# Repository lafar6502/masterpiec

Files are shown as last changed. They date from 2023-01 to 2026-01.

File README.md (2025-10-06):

# masterpiec

## Summary
Masterpiec is an arduino-based pellet and coal burner controller. It automates the burning process and controls temperatures of central heating and hot water boiler. 
The software runs on Arduino Mega 2560 and drives the fuel feeder, blower fan and water pumps (central heating, hot water boiler and hot water circulation). The control is optimized for fuel efficiency and clean burn. Masterpiec can be adapted to multiple types of pellet and coal burners with automatic fuel feed, and is pretty simple to build as a DIY project. 
## 
## Aktualizacje

[Lista ostatnich zmian](updates.md)

## Co to jest, zasada działania
Masterpiec to kompletny sterownik pieca CO z podajnikiem działający w oparciu o algorytm 'trójstanowy'.
Polega to na tym że spalanie odbywa się w trzech trybach: duża moc, niska moc oraz postój. Sterownik stara się nie wchodzić w tryb postoju w miarę możliwości, zamiast tego pracuje
w trybie ciągłym przełączając się między wysoką a niską mocą. 

Ustawienia dla mocy wysokiej i niskiej są konfigurowalne i powinny być dobrane doświadczalnie, w zależności od możliwości palnika w kotle oraz od zapotrzebowania instalacji na ciepło. Założenie jest takie że tryb wysoki powinien dawać moc wyższą niż instalacja jest w stanie odbierać (czyli że piec będzie w stanie podgrzewać wodę w instalacji mimo ciągłego odbioru ciepła), a tryb niskiej mocy powinien być poniżej średniego zapotrzebowania instalacji na ciepło (czyli że podczas pracy w tym trybie temperatura instalacji będzie się obniżać wraz z odbiorem ciepła przez budynek). Wtedy, przełączając się między trybem wysokim a niskim sterownik jest w stanie regulować temperaturę w instalacji bez przerywania pracy kotła.

Sterownik używa tylko dwóch mocy podczas pracy, nie próbuje uzyskać innych mocy pośrednich. Dzięki temu można wyregulować ustawienia spalania tak żeby było ono poprawne w obu trybach.

## Po co powstał masterpiec
Żeby czysto i oszczędnie prowadzić proces spalania przy prostym i zrozumiałym algorytmie sterującym. Współczesne sterowniki 'PID' mają mniej lub bardziej skomplikowane algorytmy regulacji mocy, ale ich logika jest mało przejrzysta dla użytkownika a możliwości konfiguracji często mocno ograniczone. Prowadzi to w wielu sytuacjach do 'zgłupienia' sterownika i jego nieoptymalnego działania, zwłaszcza w przypadku instalacji nietypowych względem tego co zakłada producent.
Masterpiec działa w oparciu o prosty ale skuteczny algorytm którego parametry są konfigurowalne, dzięki czemu powinno być jasne dla użytkownika jak osiągnąć pożądane zachowanie kotła poprzez regulację parametrów sterowania.

Powodem dodatkowym był 'fun factor' przedsięwzięcia, czyli budowa sterownika od podstaw z możliwością samodzielnego zaprogramowania logiki według widzimisię autora. 

## zasady korzystania z kodu
Kod źródłowy jest udostępniony publicznie dla wszystkich którzy są zainteresowani poznaniem zasady działania sterownika oraz jego modyfikacją i rozbudową. Wszelkie projekty zbudowane na podstawie niniejszego kodu powinny być również udostępnione publicznie, autor nie zezwala na wykorzystanie tego kodu w projektach komercyjnych.   

## Funkcje sterownika
* pompa CO
* pompa CWU
* pompa cyrkulacji
* czujniki: temperatura CO, CWU, powrotu, temp. spalin
* podajnik
* dmuchawa - sterowanie algorytmem grupowym 
* obsługa zewnętrznego termostatu
* tryb letni (tylko CWU)
* wygaszanie i rozpalanie

## Hardware - kocioł
Masterpiec działa z kotłami z podajnikiem ślimakowym (testowany z palnikiem SV200). Dmuchawa - dowolny typ, 230V. Pompy - dowolne, 230V. Zapalarka 230V ceramiczna, dowolny model.
Niektóre pompy elektroniczne źle znoszą zewnętrzne sterowanie zasilaniem i mogą uszkodzić układ sterujący SSR (miałem jeden model Wilo który nie lubił być włączany i wyłączany przekaźnikiem, powodował uszkodzenia układu sterującego zasilaniem). Ale np 'inteligentne' pompy Grundfos pracują bezproblemowo.

## komponenty sterownika
* Arduino Mega
* Shield SD card
* 8-kanałowy moduł przekaźników SSR z detekcją zera
* wyświetlacz i2c, enkoder
* moduł RTC
* czujniki temperatury (3 szt DS18B20 oraz 1 lub 2szt MAX6675)
* przepływomierz samochodowy (MAF) - opcjonalnie

Sterownik jest zbudowany z gotowych modułów, nie wymaga robienia własnych płytek drukowanych ani wykonywania skomplikowanych układów elektronicznych. Potrzebna jest podstawowa umiejętność używania lutownicy i innych narzędzi oraz zrozumienie zasad łączenia urządzeń elektrycznych.

[Schemat połączeń komponentów](SCHEMATIC.md)

## Funkcje poprawiające jakość pracy kotła
- funkcja dopalania - przy zmniejszaniu mocy lub przechodzeniu w postój piec przeprowadza dodatkowy cykl dopalania nadmiaru opału, dzięki czemu zmniejsza się ilość wytwarzanej sadzy
- rozpalanie zawsze na wysokiej mocy przy wznawianiu pracy po postoju, dzięki czemu temperatura żaru rośnie szybko i zmniejsza się dymienie
- dobra współpraca z termostatem pokojowym, algorytm jest dostosowany do zewnętrznego sterowania i nie destabilizuje się przy niespodziewanych zmianach zapotrzebowania na ciepło
- zabezpieczenie przed przekraczaniem temp zadanej (poprzez zmniejszenie mocy z wyprzedzeniem)
- cyrkulacja w trybie ciągłym lub załączanie cykliczne w celu ograniczenia strat ciepła
- utrzymywanie stałego przepływu powietrza na podstawie wskazań czujnika MAF

## Funkcje planowane, do realizacji lub rozważenia
- zewnętrzne sterowanie załączeniem kotła, do współpracy z pompą ciepła (kocioł załącza się gdy temperatura powietrza jest za niska dla efektywnej pracy pompy, dzięki czemu pompa ciepła nie musi używać grzałek elektrycznych)
- zewnętrzne sterowanie pompami CO i CWU, też w celu współpracy z pompą ciepła zasilającą instalację przez wymiennik płytowy (gdy pompa ciepła działa to masterpiec załącza pompę CO lub CWU żeby był przepływ w obu obiegach wymiennika).
- sterowanie zaworem mieszającym
- sterowanie zaworem przełączającym trójdrożnym (CO/CWU) - dla instalacji posiadającej tylko jedną pompę obiegową.
- obsługa bufora ciepła
- sterowanie prędkością pracy pompy CO za pomocą PWM, w celu kontroli ilości ciepła odbieranego z kotła/wymiennika płytowego

## MAF - wykorzystanie samochodowego przepływomierza

[Poradnik MAF](MAF.md)

## Ekrany

Ekr 1.
```
 ; jesli termostat 
 v
T:45.3/50 B:42.1
_1 25 0.2
^
| _ - brak grzania, ! - CO, @ - bojler, | - blokada pieca  
```

## Podziękowania, inspiracje

Główną inspiracją dla masterpieca był Lucjan - czyli sterownik kotła w wersji DIY udostępniony przez UZI18 

https://github.com/uzi18/sterownik

To dzięki ekipie Lucjana zobaczyłem że budowa sterownika nie jest aż tak trudnym przedsięwzięciem. 
Masterpiec zaczął się jako próba zbudowania Lucjana. Próba zakończona powodzeniem, jednak okazało się że Lucjan nie do końca realizuje zadania które chciałem żeby realizował. Z uwagi na to że Lucjan nie udostępnia kodu źródłowego i nie umożliwia samodzielnej modyfikacji logiki sterownika postanowiłem stworzyć alternatywne oprogramowanie od zera.
Masterpiec opiera się na tych samych komponentach hardware-owych co Lucjan, czyli Arduino Mega, popularnych czujnikach temperatury oraz dostępnych na rynku modułach wykonawczych. Dzięki pracy ekipy Lucjana nie musiałem tych komponentów dobierać samodzielnie, co prawdopodobnie nie udało by się nigdy. 

Konsekwencją powyższego jest to że masterpiec jest w dużym stopniu zgodny hardware-owo z Lucjanem i posiadając Lucjana można go przekonwertować na masterpiec/i w drugą stronę - choćby w celu porównania funkcji i wybrania lepiej sprawdzającego się rozwiązania. Nie ma 100% zgodności, ale różnice są niewielkie i dotyczą innych numerów pinów GPIO - być może zostanie to poprawione w przyszłości. 

Najważniejszą różnicą jest to że Masterpiec udostępnia kod źródłowy i umożliwia samodzielną modyfikację. Masterpiec jest też prostszy, realizuje mniej funkcji i nie oferuje wielu różnych wariantów hardware-u. Zdecydowanie zachęcam tutaj do wypróbowania zarówno Masterpieca jak i Lucjana i dziękuję ekipie Lucjana za pracę włożoną w ten ciekawy projekt.

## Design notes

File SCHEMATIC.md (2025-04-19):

## Zestawienie połączeń GPIO Arduino z pozostałymi modułami.

1) Nie wymieniamy tu pinów GND - wszystkie elementy mają wspólne GND.

2) VCC - zasilanie Arduino oraz komponentów +5V. 
Arduino zasilamy poprzez wejście zasilania, albo podłączając zasilacz 9V do pinu VIN.
Pozostałe komponenty wymagające zasilania VCC +5V zasilamy z pinu +5V Arduino. Arduino odpowiada za dostarczenie napięcia +5V.

3) Część sterującą można połączyć bez lutowania (kabelki połączeniowe i złącza pin), ale jeśli sterownik ma działać niezawodnie przez długi czas to połączenia lutowane są lepsze.

| Pin Arduino | Drugi koniec |
| --- | --- |
|  | *Moduł wykonawczy SSR* |
| 2 | DET - detekcja 0 |
| A9 | Pompa CO |
| A10 | Podajnik |
| A11 | Pompa cyrkulacji |
| A13 | Dmuchawa |
| A14 | POMPA CO 2 |
| A15 | POMPA CWU | 
|  | *Termostat* |
| 47 | Termostat we |
| 26 | Termostat alternatywne wejscie (NC) |
|  | *Termopara/czujnik spalin* |
| 39 | MAX 6675 SCK |
| 40 | MAX 6675 SO |
| 41 | MAX 6675 CS |
|  | *czujniki DALLAS DS18B20* |
| 22 | DATA |
|  | *Enkoder* |
| 15 | PIN A |
| 18 | PIN B |
| 34 | Przycisk |
|  | *Wyswietlacz I2C oraz moduł RTC*|
| 20 SDA | SDA |
| 21 SCL | SCL |

## Podłączenie wyświetlacza i RTC
Oba moduły komunikują się przez I2C i korzystają z tych samych pinów. Moduł RTC jest 'przelotowy' czyli można wyświetlacz podłączyć do niego.

## Podłączenie czujników DS18B20
Łączymy je równolegle. Złącze DATA - na pin 22 Arduino.
Dodatkowo VCC i GND. Między VCC a Data należy dać rezystor 3.3K

## Podłączenie termopary MAX 6675
Wykorzystuje interfejs SPI wbudowany w Arduino
Czasami konieczne jest dodatkowe połączenie '-' termopary z gnd - gdy brak odczytu lub dostajemy jakieś bezsensowne odczyty.

## Zestawienie Modułów

| Moduł | Liczba szt | Informacje |
| --- | --- | --- |
| Arduino 2560 Mega | 1 | klon zupełnie wystarcza |
| Ethernet shield W5100 | 1 | Aktualnie nie używamy ethernetu, wyłącznie karty SD. Ale warto mieć możliwość podłączenia sieci |
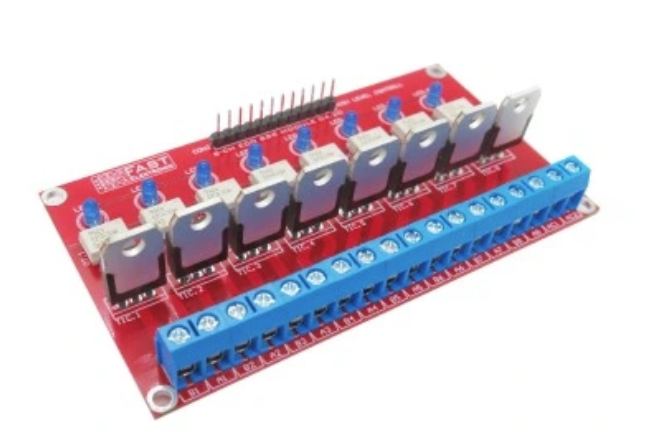
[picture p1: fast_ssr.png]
moduł ssr
| Moduł Przekaźnika 8x SSR Triaki Detekcja 0 ARDUINO | 1 | z firmy Fast Electronic (dostępne z Allegro) wybrać z optotriakiem MOC3021 choć druga wersja MOC3041 też powinna działać  . Istotna jest funkcja detekcji zera do sterowania dmuchawą, dlatego został wybrany ten moduł. Można użyć innego ale wtedy trzeba zapewnić detekcję zera osobnym modułem.  |
| Zegar RTC DS1307 | 1 | |
| Wyświetlacz LCD 2x16 I2C | 1 | komplet z konwerterem i2c |
| Enkoder | 1 | Dowolny z przyciskiem |
| Czujnik temperatury DS18B20 | 4 | czujniki z kablem, wybrać kable odpowiedniej długości (temp CO, temp CWU, temp. powrotu, temp podajnika) |
| MAX 6675 | 1 | moduł termopary z termoparą 400st, ale może też być 600 lub 800 stopni |
| Zasilacz 9V | 1 | zasilacz dla arduino (od 7.5 do 10V, 10W powinno wystarczyć) |
| Gniazdo AC komputerowe 3pin | 5 | zasilanie pomp, podajnika, dmuchawy |
| Zabezpieczenie STB | 1 | Wyłącznik bimetaliczny NC 90 stopni C |

## Połączenia 230V oraz zasilanie

Połączenia 230V obejmują sterowanie zasilaniem pomp, podajnika, dmuchawy poprzez wyjścia modułu wykonawczego SSR.
Dodatkowo z wejścia 230V zasilany jest też zasilacz 9V dla Arduino. Tylko w w/w elementach występuje napięcie 230V, dobrze jest sekcję 230V oddzielić od pozostałej części sterownika która działa na niskim napięciu. Zapewnić odpowiednią izolację połąćzeń 230V, taśma PCV potrafi się odklejać przy pracy w wyższej temperaturze - nie polecam.
Wygodnie jest użyć komputerowego wejścia zasilania z wyłącznikiem i bezpiecznikiem.

Uwaga: nie precyzuję tu które kanały modułu wykonawczego mają być przypisane do poszczególnych urządzeń - pomp, podajnika, dmuchawy. Jest to dowolne, ale należy pamiętać o połączeniu wybranych kanałów z odpowienim pinem arduino wg rozpiski wyżej.

## Uruchamianie sterownika

Zalecam podejście krok po kroku:

1. Zasilanie Arduino 9v oraz połączenie USB z laptopem. Kompilujemy i wgrywamy masterpiec do Arduino. Program powinien wystartować (na porcie szeregowym będą komunikaty)
2. Podłączenie wyświetlacza, RTC oraz enkodera. Po uruchomieniu Masterpiec powinien wyświetlać cokolwiek na ekranie, enkoder powinien pozwalać poruszać się po menu. Prawdopodobnie na początku będzie alarm o braku czujnika temperatury.
3. Komunikaty diagnostyczne są wypisywane na port szeregowy
4. Podłączenie czujników Dallas. Po podłączeniu konieczne jest wejście w menu zaawansowane i przypisanie ról poszczególnym czujnikom (identyfikacja który jest CO, CWU itd). Upewnić się że mamy odczyt temperatury. Robimy to raz bo później ustawienia są pamiętane w EEPROM.
5. Podłączenie modułu wykonawczego SSR. Detekcja zera jest istotna, bez niej nie będzie działać sterowanie dmuchawą - czyli moduł należy podłączyć do napięcia sieciowego 230V. Można testować bez podłączania zasilanych urządzeń, są diody wskazujące stan poszczególnych wyjść.
6. Podłączenie termopary, upewnienie się że mamy odczyt temp spalin.
7. Po upewnieniu się że wszystkie komponenty działają możemy podłączyć sterownik do pieca.
8. Zabezpieczenie STB - wyłącznik montujemy na wyjściu gorącej wody z kotła, połączone w szereg w obwodzie zasilania dmuchawy (uwaga 230v)

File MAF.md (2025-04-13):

## Co to jest MAF i w jaki sposób go wykorzystujemy
MAF Sensor to przepływomierz wykorzystywany w układach dolotowych silników samochodowych - mierzy ilość przepływającego do silnika powietrza w jednostce czasu.
Po zainstalowaniu na dmuchawie można go wykorzystać także do pomiaru ilości powietrza wchodzącego do kotła oraz, w konsekwencji, do sterowania szybkością pracy dmuchawy tak żeby ilość powietrza była prawidłowa.

## Jak działa MAF
MAF opiera swoje działanie na pomiarze szybkości chłodzenia rozgrzanego drucika przez opływające powietrze. Oznacza to ze nie ma żadnych części ruchomych.
Jeśli chodzi o komunikację (sposób przekazywania pomiarów), MAFy mogą wykorzystywać różne techniki:
1. napięcie - najprostszy, starszy typ MAF. Na wyjściu czujnika jest generowane napięcie z zakresu 0..5V proporcjonalne do szybkości przepływu powietrza
2. częstotliwość - MAF generuje impulsy o częstotliwości zależnej od szybkości przepływu
3. szerokość pulsu (?) - nie wiem czy takie występują
4. cyfrowe -np Bosch  i inne. Nie udało mi się ustalić jak działa komunikacja z nimi.

## Jaki MAF dla Masterpiec
Używamy MAF typu 'napięciowego' tzn takiego który generuje napięcie proporcjonalne do szybkości przepływu. Są to czujniki spotykane w starszych samochodach, można je znaleźć np w Ford-ach (Mondeo, KA). Mają złącze z czterema przewodami, natomiast na wtyczce są często umieszczone symbole ABCD lub EABCDF oznaczające poszczególne wyprowadzenia. Używane czujniki tego typu można łatwo kupić w cenie ok 10 PLN.<br>
Generalnie powinniśmy wybierać MAFy od silników o niskiej pojemności bo czujniki te są przystosowane do mniejszych przepływów powietrza i dają dzięki temu dokładniejsze wyniki pomiaru. 

MAF FORD - Wyprowadzenia przedstawiają się tak: <br>
A - zasilanie +12V<br>
B - GND<br>
C - GND<br>
D - sygnał czujnika 0..5V - odczytywany przez wejście analogowe Arduino, np A0<br>
Przykładowe numery części: 97BP-12B579-AA,96FP-12B579-AB

Żeby przetestować ten typ MAF wystarczy zasilanie 12V i woltomierz -badamy napięcie na pinie wyjściowym oraz, dmuchając do przepływomierza, sprawdzamy czy napięcie odpowiednio się zmienia. Pobór prądu podczas pracy powinien być na poziomie 10mA.



MAF Bosch <br/>
Bosch produkuje MAFy w wersji analogowej (sygnał napięciowy) albo cyfrowej.
Wyprowadzenia w 4-pinowym Boschu analogowym przedstawiają się tak (piny 1 2 3 4):<br/>
1 - GND<br>
2 - sygnał - (może być GND)<br>
3 - +12V<br>
4. sygnał + <br>
Interesuje nas różnica napięć między pin 2 i 4, ale w sumie wystarczy różnica między GND a pin 4.<br>

Dla 5-pinowych Bosch:<br>
1 - NTC (czujnik temperatury) - ignorujemy<br>
2 - +12V <br>
3 - GND<br>
4. +5V<br>
5. Wyjście czujnika 0..5V<br>

Przykładowe numery części Bosch:
(4 pin) 0 280 217 111 (4pin), 0 280 217 102, 0 280 217 120, 0 280 217 519, 0 280 217 801, 0 280 217 107<br>
(5 pin) 0 280 217 123,  0 280 218 019,  0 280 217 531, 0 280 218 008, 0 281 002 421 <br> 
0 280 217 123 (5pin), 0 280 218 037 (5pin), 0 280 218 116 (5 pin), 0 280 218 335 (5 pin),  0 280 218 088, 0 280 218 440 (5 pin), <br>
0 280 218 446, 0 280 218 089, 

## MAF typ 2 - częstotliwość
Drugi potencjalnie łatwy do zastosowania rodzaj MAFa to grupa 2, tj sterujący częstotliwością impulsu.
W tej chwili Masterpiec nie używa tego typu przepływomierzy, ale jest szansa na ich wykorzystanie w przyszłości.

## MAF typ 3 - szerokość pulsu
Uzupełnię gdy znajdę przykład

## MAF typ 4 - cyfrowy
Bosch produkuje takie MAFy, na pierwszy rzut oka nie różnią się niczym od wersji z grupy 1 ale wyniki pomiaru są dostarczane w postaci cyfrowej. Protokół komunikacyjny nie jest mi znany i nie ma dokumentacji. Nie będziemy takich wykorzystywać w masterpiec.

## Inne MAFy
W szczególności firmy 'continental', 'siemens' - stosowane w różnych samochodach. Mają także 4 wyprowadzenia, ale nie udało mi się zidentyfikować sposobu ich podłączenia ani zasady działania.
Uwaga: zalecana ostrożność w podłączaniu do Arduino, w nieznanym typie MAF na wyjściach może pojawić się np napięcie 12V które doprowadzi do uszkodzenia arduino.
Dotyczy wszystkich MAFów.

## Zasilanie MAF

MAFy samochodowe są przystosowane do zasilania napięciem 12V (a konkretnie ok 14V) więc można wykorzystać zasilacz 12V do zasilania zarówno MAFa jak i Arduino.
Natomiast bez problemu powinno dać się też pracować z zasilaczem 9V bo MAFy mają dość szerokie dopuszczalne napięcie zasilania, z przedziału mniej-więcej 8.5V do 17V.
Pobór prądu przez MAF powinien być w  okolicach 10-15mA.

## Wykorzystanie czujnika przepływu do sterowania spalaniem

Odczyt przepływu powietrza działa podczas pracy dmuchawy. Gdy dmuchawa nie pracuje MAF jest wyłączany (zakładam że nie jest to czujnik przeznaczony do pracy 24/7).
Podawana przez czujnik wartość przepływu nie jest wyrażona w żadnych jednostkach, jest to po prostu odczyt napięcia z czujnika.

Standardowo wartość napięcia odczytywana przez Arduino może być z przedziału 0...1023 gdzie 1023 odpowiada napięciu 5V. Czujnik MAF nie osiąga 5V na wyjściu, zwykle są to napięcia z zakresu 2-3.5V - dlatego dokonujemy przeskalowania wyniku pomiaru do docelowej wartości z zakresu 0..255 (0 - brak przepływu, 255 - maksymalny możliwy przepływ).

Parametr "MAF Skala" określa skalowanie - Flow = odczyt napięcia * 255 / (4 * MAF_Skala + 3) <br>
Np MAF Skala=160 oznacza że masterpiec będzie widział maksymalny przepływ (Flow = 255) gdy odczyt z pinu A0 da wartość 160*4 + 3 = 643. Co odpowiada napięciu ok 3.15V z MAFa. Dobieramy MAF Skala tak żeby wartość Flow = 255 była maksymalnym możliwym do uzyskania na naszej dmuchawie przepływem.

MAF Skala należy dobrać doswiadczalnie zależnie od posiadanego MAFa

--
* https://www.msextra.com/doc/pdf/html/MS3baseV30_Hardware-1.5.pdf/MS3baseV30_Hardware-1.5.html
* [Bosch HFM5 Sensors.pdf](./Bosch%20HFM5%20Sensors.pdf)

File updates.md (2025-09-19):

2022-06-27

* Obsługa samochodowego czujnika MAF do pomiaru ilości powietrza
* Funkcja korekcji prędkości dmuchawy w czasie pracy w oparciu o odczyt MAF
* Zmiana połączeń arduino-peryferia (zmiany numerów pinów) z powodu reorganizacji kabelków

2022-06-19

* Obsluga zapalarki (glownie ze wzgledu na pellet, ale z ekogroszkiem tez powinno dzialac)
* Automatyczne rozpalanie i wygaszanie <br>Możliwość ustawienia czy piec ma się rozpalać i wygaszać automatycznie, czy nie.
* Obsługa max 3 zestawów ustawień między którymi można się przełączać (np gdy mamy kocioł na ekogroszek i pellet)<br> Uwaga: po zmianie aktywnego banku ustawień nalezy zrobić restart sterownika - wtedy zostaną wczytane te z nowo wybranego banku. Gdy po zmianie numeru banku nie zrobisz restartu, tylko np zmienisz jeszcze jakiś parametr, to aktualne ustawienia nadpiszą te w wybranym banku (czyli można w ten sposob skopiować ustawienia)
* ulepszone wykrywanie wygasnięcia ognia<br>Z uwzględnieniem temperatury spalin
* Wykrywanie rozpalenia ognia<br>W oparciu o wzrost temperatury spalin

2025-wiosna
* dodana możliwość zewnętrznego sterowania pompami CO i CWU
  To realizuje scenariusz gdy do instalacji jest wpięta pompa ciepła za pośrednictwem wymiennika płytowego (czyli pompa ciepła ma własny obieg. Na podstawie sygnałów pracy z pompy ciepła załączana jest albo pompa CO, albo pompa CWU, tak żeby     był przepływ wody przez wymiennik.

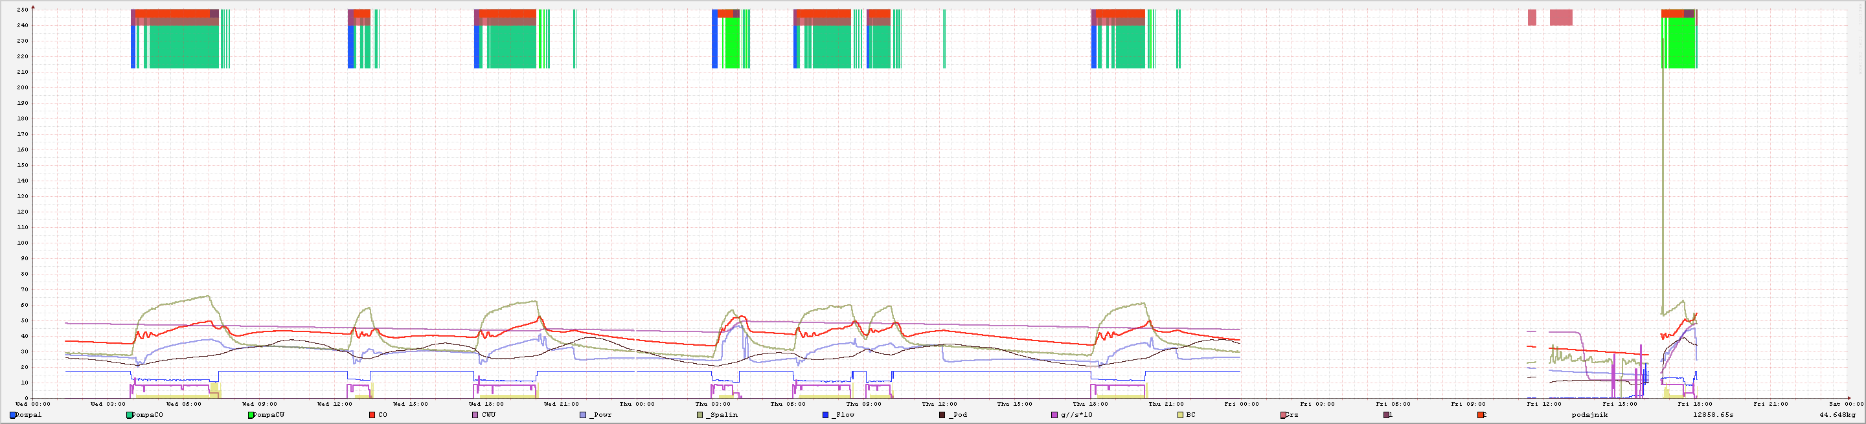
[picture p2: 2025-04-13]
rrd_graphs/out.gif

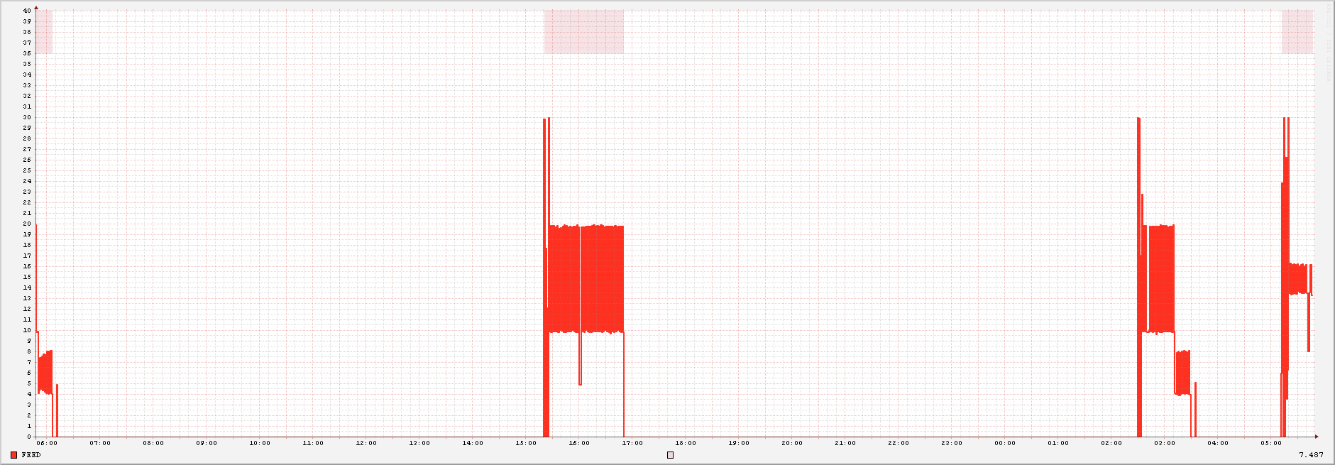
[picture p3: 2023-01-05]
rrd_graphs/fuel.gif

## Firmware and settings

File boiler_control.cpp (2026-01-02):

#include <arduino.h>
#include "hwsetup.h"
#include "piec_sensors.h"
#include "boiler_control.h"
#include "global_variables.h"
#include "digitalWriteFast.h"


#define KICKSTART_MIN 10 //minimum pulses/sec - below that we run a kickstart

struct tPowerControlPin {
  uint8_t Pin;
  uint8_t Mask;
  bool    Enabled;
  bool    On;
};

//flags for synced turning on/off of port K bits
volatile uint8_t g_powerFlags = 0;
volatile uint8_t g_powerBits = 0;
int8_t g_BlowerPowerCorrection = 0; //blower power adjustment for current burn state. we adjust this adjustment when correcting flow.

//PINTK, PO
#define POWER_PORT_MASK 0b11111111

tPowerControlPin pump_ctrl_pins[] = {
  {HW_PUMP_CO1_CTRL_PIN,  MASK_PUMP_CO1, false},
  {HW_PUMP_CWU1_CTRL_PIN, MASK_PUMP_CWU1, false},
  {HW_PUMP_CO2_CTRL_PIN, MASK_PUMP_CO2, false},
  {HW_PUMP_CIRC_CTRL_PIN, MASK_PUMP_CIRC, false},
 
  {HW_FEEDER_CTRL_PIN, MASK_FEEDER, true},
  {HW_BLOWER_CTRL_PIN, MASK_BLOWER, true},
  
};

unsigned long g_FeederRunTime = 0;
unsigned long g_LastFeederStart = 0;


void setTriacOutOn(uint8_t num) {
  g_powerFlags |= pump_ctrl_pins[num].Mask;
}

void setTriacOutOff(uint8_t num) {
   g_powerFlags &= ~pump_ctrl_pins[num].Mask;
}

bool isTriacOutOnNow(uint8_t num) {
  return (PINC & pump_ctrl_pins[num].Mask) != 0;
}

void setPumpOn(uint8_t num) {
  if (num >= sizeof(pump_ctrl_pins)/sizeof(tPowerControlPin)) return;
  pump_ctrl_pins[num].On = true;
  setTriacOutOn(num);
  //digitalWrite(pump_ctrl_pins[num].Pin, HIGH);
}

void setPumpOff(uint8_t num) {
  if (num >= sizeof(pump_ctrl_pins)/sizeof(tPowerControlPin)) return;
  pump_ctrl_pins[num].On = false;
  setTriacOutOff(num);
  //g_powerFlags &= ~pump_ctrl_pins[num].Mask;
  //digitalWrite(pump_ctrl_pins[num].Pin, LOW);
}

bool isPumpOn(uint8_t num) {
  if (num >= sizeof(pump_ctrl_pins)/sizeof(tPowerControlPin)) return false;
  //return pump_ctrl_pins[num].On;
  
  //return digitalRead(pump_ctrl_pins[num].Pin) != LOW;
  return isTriacOutOnNow(num);
}

bool isPumpEnabled(uint8_t num) {
  if (num >= sizeof(pump_ctrl_pins)/sizeof(tPowerControlPin)) return false;
  return true;
}


void setFeeder(bool on) {
  bool pr = (g_powerFlags & MASK_FEEDER) != 0;
  if (on) 
    g_powerFlags |= MASK_FEEDER;
  else
    g_powerFlags &= ~MASK_FEEDER;
  
  if (pr == on) return; // no change of state
  
  unsigned long m = millis();
  
  if (on) {
    g_LastFeederStart = m;  
  } else {   
    g_FeederRunTime += (m - g_LastFeederStart);
    g_LastFeederStart = m;
    Serial.print(F("Feed stop. run time ms "));
    Serial.println(g_FeederRunTime);
  }
}

//uruchomienie podajnika
void setFeederOn() {  
  setFeeder(true);
}
//zatrzymanie podajnika
void setFeederOff() {
  setFeeder(false);
}
//czy podajnik działa
bool isFeederOn() {
  return (PINC & MASK_FEEDER) != 0;
 //return digitalReadFast(HW_FEEDER_CTRL_PIN) != LOW;
}

void setSV2HeatingPin(bool b) {
  if (HW_SV2_HEATING_PIN == 0) return;
  digitalWriteFast(HW_SV2_HEATING_PIN, HW_SV2_PIN_ACTIVELOW ? !b : b);
}

bool getSV2HeatingPin() {
  return digitalReadFast(HW_SV2_HEATING_PIN) != LOW;
}

unsigned long g_heaterStartTimeMs = 0;

bool isHeaterOn() {
  //return digitalReadFast(HW_HEATER_CTRL_PIN) != LOW;
  return (PINC & MASK_HEATER) != 0;
}
void setHeater(bool on) {
   //digitalWriteFast(HW_HEATER_CTRL_PIN, b ? HIGH : LOW);
   bool b = isHeaterOn();
  if (on) 
  {
    if (!b) g_heaterStartTimeMs = millis();
    g_powerFlags |= MASK_HEATER;
  }
  else
  {
    g_powerFlags &= ~MASK_HEATER;
  }
}

unsigned long getHeaterRunningTimeMs() {
  bool b = isHeaterOn();
  if (!b) return 0;
  return millis() - g_heaterStartTimeMs;
}

void triacOn() {
  digitalWriteFast(HW_BLOWER_CTRL_PIN, HIGH);
}

void triacOff() {
  digitalWriteFast(HW_BLOWER_CTRL_PIN, LOW);
}

//pulse count. We will reset it on every change of output power. It is used in kickstart mode.
volatile uint32_t counter;
volatile uint32_t power_counter; 

float brese_increment = 0.0;
float brese_error = 0.0;
uint8_t brese_cycle = 1;
uint8_t brese_curV = 0;
uint8_t power_set = 0;
uint8_t kickstartCount = 0;

//1 - triac on, 0 - triac off
uint8_t breseControlStep() 
{
  uint8_t rem = counter % brese_cycle;
  static uint8_t skipper = 0;
  
  if (rem == 0) {
    brese_error += brese_increment;
    brese_curV = round(brese_error);
    brese_error -= brese_curV;
  }
  uint8_t b = brese_curV > rem ? 1 : 0;
  if (isFlowTooHigh()) {
    uint8_t m = g_CurrentConfig.AirControlMode - AIRCONTROL_HITMISS0 + 1;
    if (m > 1 && m <= 4) {
        if (b != 0) {
          skipper++;
          return (skipper % m) == 0;
        }
    }
    return 0;
  }
  return brese_curV > rem ? 1 : 0;
}




 void zeroCrossHandler2() {
  counter++;
  g_powerBits = PINC & POWER_PORT_MASK;
  uint8_t pcBits = PINL;
  uint8_t stp = breseControlStep();
  if (kickstartCount > 0 && power_set > 0) {
     stp = 1;
     kickstartCount--;
  }
  if (stp) {
    power_counter++;
    g_powerFlags |= MASK_BLOWER;
  }
  else {
    g_powerFlags &= ~MASK_BLOWER;
  }
  PORTC = g_powerFlags & POWER_PORT_MASK; //put all bits at once
  if (power_set == 0 && !getManualControlMode())
    PORTL = pcBits & ~MASK_FLOW_PWR;
  else
    PORTL = pcBits | MASK_FLOW_PWR;
 }



//power in % 0..255 (255 = 100%), cycleLength 1..255
void breseInit(uint8_t power, uint8_t cycleLength) {
  kickstartCount = 0;
  if (power == 0) g_BlowerPowerCorrection = 0;
  float p0 = power + g_BlowerPowerCorrection;
  if (p0 < 0) p0 = 0;
  if (p0 > 255) p0 = 255;
  float powerPerc = p0 * (g_CurrentConfig.BlowerMax == 0 ? 1.0 : (float) g_CurrentConfig.BlowerMax / 255.0);
  if (power_set == 0) {
    counter = 0;
    power_counter = 0;    
    kickstartCount =  power > 0 && powerPerc < KICKSTART_MIN ? KICKSTART_MIN : 0;
  };
  power_set = power;
  brese_increment = powerPerc * cycleLength / 255.0;
  brese_cycle = cycleLength;
}

int8_t getBlowerPowerCorrection() {
  return g_BlowerPowerCorrection;
}
void   setBlowerPowerCorrection(int8_t c) {
  g_BlowerPowerCorrection = c;
  breseInit(power_set, brese_cycle);
}


void initializeBlowerControl() {
  Serial.println("init gpio");
  delay(2000);
  brese_cycle = g_DeviceConfig.DefaultBlowerCycle;
  pinModeFast(HW_BLOWER_CTRL_PIN, OUTPUT);
  triacOff();
  pinMode(HW_ZERO_DETECT_PIN, INPUT);
  pinMode(HW_PUMP_CO1_CTRL_PIN, OUTPUT);
  pinMode(HW_PUMP_CWU1_CTRL_PIN, OUTPUT);
  pinMode(HW_PUMP_CO2_CTRL_PIN, OUTPUT);
  pinMode(HW_PUMP_CIRC_CTRL_PIN, OUTPUT);
  pinMode(HW_FEEDER_CTRL_PIN, OUTPUT);
  pinMode(HW_HEATER_CTRL_PIN, OUTPUT);
  pinMode(HF_FLOW_SENSOR_POWER_PIN, OUTPUT);
  pinMode(HW_SV2_HEATING_PIN, OUTPUT);
  
  digitalWrite(HW_PUMP_CO1_CTRL_PIN, LOW);
  digitalWrite(HW_PUMP_CWU1_CTRL_PIN, LOW);
  digitalWrite(HW_PUMP_CO2_CTRL_PIN, LOW);
  digitalWrite(HW_PUMP_CIRC_CTRL_PIN, LOW);
  digitalWrite(HW_FEEDER_CTRL_PIN, LOW);
  digitalWrite(HW_HEATER_CTRL_PIN, LOW);
  digitalWrite(HF_FLOW_SENSOR_POWER_PIN, LOW);
  digitalWrite(HW_SV2_HEATING_PIN, HW_SV2_PIN_ACTIVELOW ? HIGH : LOW);
  if (ALERT_STATE_PIN != 0) {
    pinMode(ALERT_STATE_PIN, OUTPUT); //low: alert state
    digitalWrite(ALERT_STATE_PIN, LOW);
  }
  
  if (HW_THERMOSTAT_PIN != 0) 
  {
    pinMode(HW_THERMOSTAT_PIN, g_CurrentConfig.EnableThermostat == 2 ? INPUT : INPUT_PULLUP);  
  }
  if (HW_THERMOSTAT_PIN_ALT != 0) 
  {
    pinMode(HW_THERMOSTAT_PIN_ALT, INPUT); 
  }
  attachInterrupt(digitalPinToInterrupt(HW_ZERO_DETECT_PIN), zeroCrossHandler2, RISING);  
  if (FURNACE_ENABLE_PIN != 0) {
    pinMode(FURNACE_ENABLE_PIN, INPUT_PULLUP); //pull up by default
    if (g_CurrentConfig.ExtFurnaceControlMode != 0) {
      int mode = g_CurrentConfig.ExtFurnaceControlMode % 2 == 0 ? INPUT_PULLUP : INPUT;
      pinMode(FURNACE_ENABLE_PIN, mode);
      Serial.print("pin piec:");
      Serial.print(FURNACE_ENABLE_PIN);
      Serial.print(" mode:");
      Serial.print(mode);
      Serial.println();
    }
  }
  
  if (g_CurrentConfig.ExtPumpControlMode != 0) {
    int mode = g_CurrentConfig.ExtPumpControlMode % 2 == 0 ? INPUT_PULLUP : INPUT;
    if (PUMP_CO_EXT_CTRL_PIN != 0) {
      pinMode(PUMP_CO_EXT_CTRL_PIN, mode);
      Serial.print("pin co: ");
      Serial.print(FURNACE_ENABLE_PIN);
      Serial.print(" mode:");
      Serial.print(mode);
      Serial.println();
    }
    if (PUMP_CW_EXT_CTRL_PIN != 0) {
      pinMode(PUMP_CW_EXT_CTRL_PIN, mode);
      Serial.print("pin cw: ");
      Serial.print(PUMP_CW_EXT_CTRL_PIN);
      Serial.print(" mode:");
      Serial.print(mode);
      Serial.println();
    }
    Serial.print("pullup:");
    Serial.print(INPUT_PULLUP);
    Serial.println();
  }
}


bool isThermostatOn() {
  if (HW_THERMOSTAT_PIN != 0 && (g_CurrentConfig.EnableThermostat & 0x01) != 0 && digitalReadFast(HW_THERMOSTAT_PIN) == LOW) return true;  //NO - low
  if (HW_THERMOSTAT_PIN_ALT != 0 && (g_CurrentConfig.EnableThermostat & 0x02) != 0 && digitalReadFast(HW_THERMOSTAT_PIN_ALT) == HIGH) return true; //NC
  return false;
}

uint8_t getCycleLengthForBlowerPower(uint8_t power) {
  return g_DeviceConfig.DefaultBlowerCycle;
}

void setBlowerPower(uint8_t power) {
  breseInit(power, brese_cycle == 0 ? getCycleLengthForBlowerPower(power) : brese_cycle);
}

void setBlowerPower(uint8_t power, uint8_t powerCycle) 
{
  breseInit(power, powerCycle);
}

uint8_t getCurrentBlowerCycle() {
  return brese_cycle;
}

uint8_t getCurrentBlowerPower() {
  return power_set;
}

int8_t getBlowerPowerCorrection();
void   setBlowerPowerCorrection();


unsigned long g_feederRunMs = 0;
unsigned long g_pumpCORunMs = 0;
unsigned long g_pumpCWURunMs = 0;
unsigned long g_pumpCircRunMs = 0;
//we just assume the thing has been running or not running the whole time since last check.
//so we should run this task quite frequently to avoid errors.
void gatherStatsTask() {
  static unsigned long _lastRun = 0;
  unsigned long t = millis();
  if (_lastRun != 0) {
    unsigned long rt = t - _lastRun;
    if (isFeederOn()) g_feederRunMs += rt;
    if (isPumpOn(PUMP_CO1)) g_pumpCORunMs += rt;
    if (isPumpOn(PUMP_CWU1)) g_pumpCWURunMs += rt;
    if (isPumpOn(PUMP_CIRC)) g_pumpCircRunMs += rt;  
  }
  _lastRun = t;
}

/*
volatile unsigned PulseTime = 0;
ISR(TIMER1_CAPT_vect)
{
  static unsigned RisingEdgeTime = 0;
  static unsigned FallingEdgeTime = 0;
  
  // Which edge is armed?
  if (TCCR1B & (1 << ICES1))
  {
    // Rising Edge
    RisingEdgeTime = ICR1;
    TCCR1B &= ~(1 << ICES1); // Switch to Falling Edge
  }
  else
  {
    // Falling Edge
    FallingEdgeTime = ICR1;
    TCCR1B |= (1 << ICES1); // Switch to Rising Edge
    PulseTime = FallingEdgeTime - RisingEdgeTime;
  }
}


void loop() {
  unsigned pulseTime = 0;
  noInterrupts();
  pulseTime = PulseTime;
  PulseTime = 0;
  interrupts();


  if (pulseTime)
  {
    Serial.println(pulseTime);
  }
}
*/

void initializeFlowMeter() {
#ifdef HW_FLOW_SENSOR_INPUT_PIN
  pinMode(HW_FLOW_SENSOR_INPUT_PIN, INPUT);
  Serial.print("Flow sensor in V:");
  Serial.println(HW_FLOW_SENSOR_INPUT_PIN);
#endif

#ifdef HW_FLOW_SENSOR_PULSE_PIN
  

#endif
  
}


float getCurrentFlowRate() {
#ifdef HW_FLOW_SENSOR_INPUT_PIN
  int x = analogRead(HW_FLOW_SENSOR_INPUT_PIN);
  return (float) x;
#endif
#ifdef HW_FLOW_SENSOR_PULSE_PIN

#endif
  return 0;
}

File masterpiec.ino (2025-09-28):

#include "masterpiec.h"
#include <assert.h>
#include <MD_DS1307.h>
#include "ui_handler.h"
#include "burn_control.h"
#include "piec_sensors.h"
#include "boiler_control.h"

void updateDallasSensorAssignmentFromConfig();
/**
 * struktura programu
 * - sterowanie silnikiem dmuchawy - na przerwaniu 0
 * - pętla sterowania grzaniem (tj załączanie dmuchawy i podajnika w odpowiednim reżimie) - na przerwaniu zegarowym, aktualizacja statusu co 1 sek. Pętla sterowania grzaniem obsługuje też wyłączanie i załączanie pomp.
 * - obsługa UI. Aktualizacja ekranu w głównym loop-ie, natomiast obsługa inputu - z przerwań. Nie powinno być wyswietlania czegokolwiek w przerwaniu.
 * - zewnętrzny termostat - podpięty do jednego z pinów. Odczytywany tryb (grzej / nie grzej) i obsługiwany odpowiednio w pętli sterowania grzaniem
 * - odczyt czujników temperatury - też powinien następować w pętli, nie wiem czy tak często jak pętla sterowania grzaniem
 * 
 * 
 * pompy - działają niezależnie. Jeśli grzanie=ON to pompa CO załącza się gdy temp. jest powyżej minimalnej i wyłącza się gdy jest poniżej. Jeśli grzanie = off to pompa CO załącza się wyłącznie po to żeby pozbyć się nadmiaru ciepła, czyli gdy temp aktualna CO jest wyższa 
 * niż TZadana + delta. Pozbywanie się nadmiaru ciepła trwa do momentu gdy temp spadnie albo gdy przestanie rosnąć albo przez ustalony cykl. Możemy też pompę co skonfigurować do załączania się cyklicznie na x minut co y minut.
 * Pompa CWU - działa gdy temp pieca jest wyższa niż temp bojlera+delta CWU (czyli to jest nasza minimalna temp załączenia pompy). Załącza się gdy temp bojlera spadnie poniżej tCWUZadana - hist1. W momencie załączenia przestawiamy TZadana pieca na tZadanaCWU+delta CWU
 * pompa CWU wyłącza się gdy temp bojlera osiągnie docelową (wtedy tez przywracamy temp zadana pieca) albo gdy temp spadnie poniżej tBojler+delta cwu.
 * 
 */
unsigned long _lastDebugTime = 0;
uint8_t _debugTime = 0;

void setup() {
  //initialize interrupts etc
  //initialize hardware
  delay(1000);
  Serial.begin(115200);
  if (!RTC.isRunning()) {
    //Serial.println("RTC not runnning, starting the clock");
    RTC.control(DS1307_CLOCK_HALT, DS1307_OFF);
  }
  RTC.readTime();
  // put your setup code here, to run once:
  readInitialConfig();
  Serial.print("CFG size:");
  Serial.println(sizeof(TControlConfiguration));  
  if (sizeof(TControlConfiguration) > CFG_SLOT_SIZE) {
    exit(0);
  }
  initializeEncoder();
  initializeDisplay();
  g_CurrentUIView = 0;
  updateView();
  initializeDallasSensors();
  initializeMax6675Sensors();
  initializeBlowerControl();
  initializeFlowMeter();
  loggingInit();
  Serial.print("Hw inited. Time:");
  Serial.print(RTC.yyyy);
  Serial.print('-');
  Serial.print(RTC.mm);
  Serial.print('-');
  Serial.print(RTC.dd);
  Serial.print('T');
  Serial.print(RTC.h);
  Serial.print(':');
  Serial.println(RTC.m);
  
  updateDallasSensorAssignmentFromConfig();
  
  for(int i=0;i<6;i++) {
    delay(500);
    refreshSensorReadings();
  }
  initializeBurningLoop();
  changeUIState('0');
  _lastDebugTime = millis();
}


void loop() {
  uint64_t m = millis();
  _debugTime = 0;
  if (m - _lastDebugTime >= 30000) {
    _debugTime = 1;
    _lastDebugTime = m;
  }
  void (*pf)(void*) = g_uiBottomHalf;
  if (pf != NULL) 
  {
    pf(g_uiBottomHalfCtx);
    if (pf == g_uiBottomHalf) 
    {
      g_uiBottomHalf = NULL;
      g_uiBottomHalfCtx = NULL;  
    }
  }
  RTC.readTime();
  refreshSensorReadings();
  burnControlTask();     
  circulationControlTask();
  gatherStatsTask();
  updateView();          
  periodicDumpControlState();
  

#ifdef MPIEC_ENABLE_SCRIPT
    handleSerialShellTask();
#endif
  loggingTask();
  commandHandlingTask();
  int m2 = millis();
  int d = 150 - (m2 - m);
  if (d > 0) 
  {
    delay(d);
  }
  else 
  {
    Serial.print(F("zabraklo mi ms "));
    Serial.println(-d);  
  }
}

extern uint32_t counter;

bool isDebugTime() {
  return _debugTime != 0;
}

void periodicDumpControlState() {
  static TSTATE pstate = STATE_UNDEFINED;
  unsigned long t = millis();
  if (isDebugTime() || g_BurnState != pstate)
  {
    pstate = g_BurnState;
    Serial.print("T+");
    Serial.print(t / 1000);
    Serial.print(F(" s:"));
    Serial.print(BURN_STATES[g_BurnState].Code);
    Serial.print(F(", dm:"));
    Serial.print(getCurrentBlowerPower());
    Serial.print(F(" ("));
    Serial.print(getCurrentBlowerCycle());
    Serial.print(F("), pd:"));
    Serial.print(isFeederOn() ? "ON": "OFF");
    Serial.print(F(", co:"));
    Serial.print(isPumpOn(PUMP_CO1));
    Serial.print(F(", cwu:"));
    Serial.print(isPumpOn(PUMP_CWU1));
    Serial.print(F(", stime:"));
    Serial.print((t - g_CurStateStart) / 1000);
    Serial.print(F(", btime:"));
    Serial.print((t - g_CurBurnCycleStart) / 1000);
    Serial.print(F(", tspalin:"));
    Serial.print(g_TempSpaliny);
    Serial.print(F(", tpiec:"));
    Serial.print(g_TempCO);
    Serial.print(F(", need:"));
    Serial.print(g_needHeat);
    Serial.print(F(", dT60:"));
    Serial.print(g_dT60);
    Serial.print(F(", dTl3:"));
    Serial.print(g_dTl3);
    Serial.print(F(", dTEx:"));
    Serial.print(g_dTExh);
    Serial.print(F(", floV:"));
    Serial.print(g_AirFlow);
    Serial.print(F(":"));
    Serial.print(g_AirFlowNormal);
    Serial.print(F(", lastT:"));
    Serial.print(g_lastCOReads.IsEmpty() ? 0.0f : *g_lastCOReads.GetAt(-1));
	  Serial.print(F(", CNT:"));
    Serial.print(counter);
    if (g_CurrentConfig.ExtFurnaceControlMode != 0 || g_CurrentConfig.ExtPumpControlMode != 0) {
      Serial.print(", OVR PO/PW/EN:");
      Serial.print(g_coPumpOverride);
      Serial.print(" ");
      Serial.print(g_cwuPumpOverride);
      Serial.print(" ");
      Serial.print(g_furnaceEnabled);   
    }
    Serial.print(", SV2:");
    Serial.print(getSV2HeatingPin());
    Serial.println();
  }
}

void updateDallasSensorAssignmentFromConfig() {
  uint8_t zbuf[8] = {0, 0, 0, 0, 0, 0, 0, 0};
  char buf[20];
  
  for(uint8_t i=0; i<8; i++) {
    uint8_t*p = g_DeviceConfig.DallasAddress[i];
    if (memcmp(p, zbuf, 8) == 0) continue;
    
    if (!ensureDallasSensorAtIndex(i, p)) {
      Serial.print(F("Invalid dallas address "));
      sprintf(buf, "%d: %02X%02X%02X%02X%02X%02X%02X%02X", i, p[0], p[1], p[2], p[3], p[4], p[5], p[6], p[7], p[8]);     
      Serial.println(buf);    
    }
  }
  for(uint8_t i=0; i<8; i++) 
  {
    printDallasInfo(i, buf);
    Serial.print(F("czujnik "));
    Serial.print(i);
    Serial.print(" ");
    Serial.println(buf);
  }
}

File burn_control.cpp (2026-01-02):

#include <arduino.h>
#include <assert.h>
#include "burn_control.h"
#include "boiler_control.h"
#include "hwsetup.h"
#include "piec_sensors.h"
#include "ui_handler.h"
#include "varholder.h"
#include <MD_DS1307.h>
#include <pid.h>

#define MAX_TEMP 90
#define FIRESTART_STABILIZE_TIME 30000



float g_TargetTemp = 0.1; //aktualnie zadana temperatura pieca (która może być wyższa od temp. zadanej w konfiguracji bo np grzejemy CWU)
float g_TempCO = 0.0;
float g_TempCWU = 0.0; 
float g_TempPowrot = 0.0;  //akt. temp. powrotu
float g_TempSpaliny = 0.0; //akt. temp. spalin
float g_TempFeeder = 0.1;
float g_TempBurner = 0;
float g_InitialTempCO = 0;
float g_InitialTempExh = 0;
float g_AirFlow = 0; //air flow measurement
volatile uint8_t g_AirFlowNormal = 0;
uint8_t g_TargetFlow; //
TSTATE g_BurnState = STATE_UNDEFINED;  //aktualny stan grzania
TSTATE g_ManualState = STATE_UNDEFINED; //wymuszony ręcznie stan (STATE_UNDEFINED: brak wymuszenia)
CWSTATE g_CWState = CWSTATE_OK; //current cw status
HEATNEED g_needHeat = NEED_HEAT_NONE; //0, 1 or 2
HEATNEED g_initialNeedHeat = NEED_HEAT_NONE; //heat needs at the beginning of current state
uint16_t g_burnCycleNum = 0; //number of burning cycles in current state
bool   g_HomeThermostatOn = true;  //true - termostat pokojowy kazał zaprzestać grzania
bool g_SV2 = false;
bool g_overrideBurning = false; //set to true to have system think fire is started
float g_TempZewn = 0.0; //aktualna temp. zewn
char* g_Alarm;
unsigned long g_P1Time = 0;
unsigned long g_P2Time = 0;
unsigned long g_P0Time = 0;

float lastCOTemperatures[21];
float lastExhaustTemperatures[21]; //every 30 sec => 10 minutes
float lastFlows[11];
uint8_t g_furnaceEnabled = 1;
uint8_t g_coPumpOverride = 0;
uint8_t g_cwuPumpOverride = 0;
unsigned long g_cwuOverrideOffTime = 0; //planned cwu override OFF time (delay..)

epid_t g_flow_pid_ctx;

CircularBuffer<float> g_lastCOReads(lastCOTemperatures, sizeof(lastCOTemperatures)/sizeof(float));
CircularBuffer<float> g_lastExhaustReads(lastExhaustTemperatures, sizeof(lastExhaustTemperatures)/sizeof(float));
CircularBuffer<float> g_lastFlows(lastFlows, sizeof(lastFlows)/sizeof(float));
//czas wejscia w bieżący stan, ms
unsigned long g_CurStateStart = 0;
//float  g_CurStateStartTempCO = 0; //temp pieca w momencie wejscia w bież. stan.
uint8_t g_BurnCyclesBelowMinTemp = 0; //number of burn cycles with g_TempCO below minimum pump temperature (for detecting extinction of fire)
unsigned long g_CurBurnCycleStart = 0; //timestamp, w ms, w ktorym rozpoczelismy akt. cykl palenia (ten podajnik+nadmuch)


TSTATE getInitialState() {
  if (g_CurrentConfig.FireStartMode == FIRESTART_MODE_DISABLED) return STATE_P0;
  if (g_CurrentConfig.FireStartMode == FIRESTART_MODE_JUSTSTOP) return STATE_FIRESTART;
  if (g_CurrentConfig.FireStartMode == FIRESTART_MODE_STARTSTOP) {
    if (g_needHeat != NEED_HEAT_NONE) return STATE_FIRESTART;
    return STATE_OFF;
  }
  return STATE_FIRESTART;
}

#define EPID_KP  2.0f
#define EPID_KI  0.15f
#define EPID_KD  0.1f
#define PID_LIM_MIN 0.0f /* Limit for PWM. */
#define PID_LIM_MAX 255.0f /* Limit for PWM. */
#define DEADBAND 0.02f /* Off==0 */

void initializeAirflowPid() {
  epid_info_t epid_err = epid_init(&g_flow_pid_ctx,
        g_AirFlowNormal, g_AirFlowNormal, g_TargetFlow,
        EPID_KP, EPID_KI, EPID_KD);

    if (epid_err != EPID_ERR_NONE) {
        Serial.print("\n\n** ERROR: epid_err != EPID_ERR_NONE **\n\n");
    }
  
}

void initializeBurningLoop() {  
  g_TargetTemp = g_CurrentConfig.TCO;
  g_HomeThermostatOn = true;
  initializeAirflowPid();
  TSTATE startState = getInitialState();
  forceState(startState);
}


void setAlarm(const char* txt) {
  if (txt != NULL) g_Alarm = txt;
  forceState(STATE_ALARM);
  
}

float g_dT60; //1-minute temp delta
float g_dTl3; //last 3 readings diff
float g_dTExh; //1-min temp delta for exhaust


const uint8_t RatioCoeffs[] = {6,4,3,2,2,1,1,1};

float CalcIncreaseRatio(const CircularBuffer<float>& buf, uint8_t numSamples) {
  uint8_t c = buf.GetCount()-1;
  if (c > numSamples) c = numSamples;
  if (c > sizeof(RatioCoeffs)/sizeof(uint8_t)) c = sizeof(RatioCoeffs)/sizeof(uint8_t);
  if (c == 0) return 0.0f;
  uint8_t coeffs = 0;
  float sum = 0.0f;
  float curVal = *buf.GetAt(-1);
  for (int i=0; i<c;i++) {
    coeffs += RatioCoeffs[i];
    float v = curVal - *buf.GetAt(-(i+2));
    v *= RatioCoeffs[i];
    v /= (i+1);
    sum += v;
  }
  return sum / coeffs;
}

float CalcIncreaseRatio2(const CircularBuffer<float>& buf, uint8_t numSamples) {
  uint8_t c = buf.GetCount()-1;
  if (c > numSamples) c = numSamples;
  if (c > sizeof(RatioCoeffs)/sizeof(uint8_t)) c = sizeof(RatioCoeffs)/sizeof(uint8_t);
  if (c == 0) return 0.0f;
  uint8_t coeffs = 0;
  float sum = 0.0f;
  float curVal = *buf.GetAt(-1);
  for (int i=0; i<c;i++) {
    coeffs += RatioCoeffs[i];
    float v = curVal - *buf.GetAt(-(i+2));
    v *= RatioCoeffs[i];
    v /= (i+1);
    sum += v;
  }
  return sum / coeffs;
}


#define AVG_CNT 4
float _tempCoAvg[AVG_CNT];
float _tempExhAvg[AVG_CNT];
uint16_t _avgIdx = 0;

#define TEMP_HISTORY_SAMPLE_TIME_MS 30000

void processSensorValues() {
  unsigned long ms = millis();
  static unsigned long prevMs = 0;
  
  float f1 = getLastDallasValue(TSENS_BOILER);
  float f2 = getLastThermocoupleValue(T2SENS_EXHAUST);
  _tempCoAvg[_avgIdx % AVG_CNT] = f1;
  _tempExhAvg[_avgIdx % AVG_CNT] = f2;
  _avgIdx++;

  g_TempCO = f1;
  g_TempSpaliny = f2;
  
  uint16_t n = _avgIdx >= AVG_CNT ? AVG_CNT : _avgIdx;
  f1 = 0; f2 = 0;
  if (n > 0) {
    for(uint16_t i =0; i<n; i++) {
      f1 += _tempCoAvg[i];
      f2 += _tempExhAvg[i];
    } 
    g_TempCO = f1 / n;
    g_TempSpaliny = f2 / n; 
  }
  
  g_TempCWU = getLastDallasValue(TSENS_CWU);
  g_TempPowrot = getLastDallasValue(TSENS_RETURN);
  g_TempFeeder = getLastDallasValue(TSENS_FEEDER);
  g_TempZewn = getLastDallasValue(TSENS_EXTERNAL);
  g_TempBurner = getLastThermocoupleValue(T2SENS_BURNER);
  g_AirFlow = getCurrentFlowRate();
  if (g_CurrentConfig.EnableThermostat) 
  {
    g_HomeThermostatOn = isThermostatOn() && g_furnaceEnabled;
  }
  if (ms - prevMs >= TEMP_HISTORY_SAMPLE_TIME_MS) {
    prevMs = ms;
    //float ts = g_TempSpaliny < g_TempCO - EXHAUST_TEMP_DELTA_BELOW_CO ? g_TempCO - EXHAUST_TEMP_DELTA_BELOW_CO : g_TempSpaliny;
    g_lastExhaustReads.Enqueue(g_TempSpaliny);
    g_lastCOReads.Enqueue(g_TempCO);
    Serial.print("Q:");
    Serial.println(g_lastCOReads.GetCount());
  }
  g_lastFlows.Enqueue(g_AirFlow);
  n = g_lastFlows.GetCount();
  float f0 = 0.0;
  for (int i=0; i<n; i++) {
    f0 += *g_lastFlows.GetAt(i);
  }
  f0 /= n;
  f1 = (float) g_DeviceConfig.AirFlowCoeff * 4.0 + 3.0;
  g_AirFlowNormal = (uint8_t) ((f0 * 255.0) / f1);

  g_dTExh = CalcIncreaseRatio(g_lastExhaustReads, 4) * 2.0;
  g_dTl3 = CalcIncreaseRatio(g_lastCOReads, 4) * 2.0;
  g_dT60 = CalcIncreaseRatio(g_lastCOReads, 8) * 2.0;
}
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

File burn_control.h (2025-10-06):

#ifndef _BURN_CONTROL_H_INCLUDED_
#define _BURN_CONTROL_H_INCLUDED_

typedef uint8_t TSTATE;



#define STATE_P0 0   //podtrzymanie
#define STATE_P1 1   //grzanie z mocą minimalną
#define STATE_P2 2   //grzanie z mocą nominalną
#define STATE_FIRESTART 3 //rozpalanie
#define STATE_ALARM 4 // alarm - cos się stało, piec zatrzymany albo włączone zabezpieczenie
#define STATE_REDUCE1 5 //tryb przejścia na niższy stan P2 => P1 => P0. zadaniem tego trybu jest dopalenie pozostałego węgla. W tym celu musimy wiedzieć z jakiego stanu wyszlismy do reduce
#define STATE_REDUCE2 6 //tryb przejścia na niższy stan P1 => P0 
#define STATE_STOP 7 //tryb ręczny - zatrzymany piec - sterowanie automatyczne powinno zaprzestać działalności 
#define STATE_OFF 8 //wygaszony
#define STATE_UNDEFINED 255

#define MAX_POWER_STATES 4 //max liczba konfiguracji dla mocy. 1 - tylko podtrzymanie, 2 - podtrzymanie i praca, 3 - podtrzymanie i 2 moce pracy, 4 - z rozpalaniem
#define MAX_PROFILES 2

typedef uint8_t CWSTATE;

#define CWSTATE_OK 1
#define CWSTATE_HEAT 2

#define NEED_HEAT_NONE 0
#define NEED_HEAT_CO   1
#define NEED_HEAT_CWU  2

#define COOLOFF_NONE 0
#define COOLOFF_OVERHEAT 1 //first mode - run cooloff only when above set temp + delta
#define COOLOFF_LOWER 2 //second mode- run cooloff while above the set temp

#define FIRESTART_MODE_DISABLED 0
#define FIRESTART_MODE_JUSTSTOP 1   //will switch off when done heating, but will not auto start
#define FIRESTART_MODE_STARTSTOP 2

//for config AirControlMode
#define AIRCONTROL_NONE 0
#define AIRCONTROL_CORRECT1 1
#define AIRCONTROL_CORRECT2 2
#define AIRCONTROL_HITMISS0 3
#define AIRCONTROL_HITMISS3 6

#define EXHAUST_TEMP_DELTA_BELOW_CO 2.0 //   

typedef uint8_t HEATNEED;

//konfiguracja jednego z poziomów mocy
typedef struct BurnParams {
    uint16_t CycleSec; //total cycle, including the fueling time, in seconds. podtrzymanie: okres przedmuchu. podawanie wegla co 1, 2, 3 przedmuchy
    //czas podawania wegla, * 10 (50 = 5 sekund)
    uint16_t FuelSecT10;
    //moc nadmuchu
    uint8_t BlowerPower; //0 .. 255 (100%)
    uint8_t BlowerCycle; //cykl dmuchawy dla zasilania grupowego. 0 gdy fazowe.
    uint8_t AirFlow; //air flow value, if zero then not used. If specified then BlowerPower is the starting power, then adjusted to AirFlow
} TBurnParams;


typedef struct DeviceConfiguration {
  uint16_t Magic; //should always be 0x6502
  uint8_t  SettingsBank;
  uint8_t DallasAddress[8][8]; //dallas sensor addresses. if zero - sensor not present
  uint8_t DefaultBlowerCycle;  
  uint8_t AirFlowCoeff;  //normalization coefficient for air flow voltage. 0 .. 255, where 255=1024 - maximum input value
} TDeviceConfiguration;

//zestaw ustawień pieca (aktualna konfiguracja). Nie zawiera bieżących wartości.
typedef struct ControlConfiguration {
  uint16_t Magic; //should always be 0x6502
  uint8_t TCO; //co temp 
  uint8_t TCWU;  //cwu temp
  uint8_t TCWU2; //cwu2 temp
  uint8_t TMinPomp; //minimum pump run temp.
  uint8_t THistCwu; //histereza cwu
  uint8_t THistCO;  //histereza co
  uint8_t TDeltaCO; //delta co - temp powyzej zadanej przy ktorej przejdzie w podtrzymanie
  uint8_t TDeltaCWU; //delta cwu - temp powyżej bojlera do ktorej rozgrzewamy piec
  uint8_t P0BlowerTime; //czas pracy dmuchawy w podtrzymaniu
  uint8_t P0FuelFreq; //podawanie wegla co x cykli przedmuchu
  bool    _delHomeThermostat;
  uint8_t SummerMode; //tryb letni = 1, tryb OFF = 2
  
  TBurnParams BurnConfigs[MAX_POWER_STATES]; //first one [0] is the podtrzymanie
  uint8_t FeederTempLimit;
  uint8_t NoHeatAlarmCycles; //time needed to deterimine if we have the fire
  uint8_t EnableThermostat; //0 disabled, 1 - NO, 2 - NC
  uint8_t CooloffTimeM10; //minutes * 10
  uint16_t CooloffPauseM10; //minutes * 10
  uint16_t FuelGrH; //fuel grams per hour of feeder work. 10 kg=10000. 
  uint16_t FuelHeatValueMJ10; //fuel heat in MJ, * 10 (100 = 10MJ)
  uint8_t  CooloffMode; //0 - none
  int8_t  FuelCorrection; //0 - none, fuel feed correction %. value=20 => make feed time longer by 20%, value = -20 - make it shorter by 20%
  uint8_t CircCycleMin; //60, 30, 15, 10, 6
  uint8_t CircWorkTimeS; //circ pump working time per cycle, sec*10 (10 = 100 sec)
  uint8_t ReductionP2ExtraTime; //in %, how much % of the P2 cycle time to add for reduction (0 = just the P2 cycle, 10 = P2 cycle + 10%)
  uint8_t BlowerMax; //Blower max value that will be our 100

  uint8_t FireStartMode; //0 - none, 1-auto off, 2 - auto on and off
  uint8_t NumFireStartCycles; //automatic firestart timeout in minutes * 10 (250 = 25 minutes). After that time we conclude 'failed to start fire' if not detected earlier
  uint8_t HeaterMaxRunTimeS; //maximum run time of the heater. If exceeded, heater will be turned off for the duration of one cycle (of STATE_FIRESTART)
  uint8_t FireDetExhDt10; //rate of exhaust temp increase to confirm ignition - divide this v by 10
  uint8_t FireDetExhIncrD10; //how much has exh temp to increase
  uint8_t FireDetCOIncr10; //how much has CO temp to increase
  uint8_t P0CyclesBeforeStandby;
  uint8_t AirControlMode; //0 - just blower %, 1 - flow meter (both % and then flow for adjustment) 2 - just the flow value is used 
  uint8_t ExtPumpControlMode; //0 disable, 1 - low signal, 2 - high signal
  uint8_t ExtFurnaceControlMode; //0 disable, 1 -low, 2 -high
  uint8_t ExtCWPumpOffDelay; //delay to switch off ext pump, * 10 sec
} TControlConfiguration;

#define CFG_SLOT_SIZE 140 //size of single config settings struct (with some extra space for future) - utility.cpp
#define DEV_CFG_SLOT_SIZE 80// size of device config record in eeprom - utility.cpp
//bieżąca konfiguracja pieca
extern TControlConfiguration g_CurrentConfig;
extern TDeviceConfiguration g_DeviceConfig;

typedef struct BurnTransition {
  TSTATE From;
  TSTATE To;
  bool (*fCondition)();
  void (*fAction)(int); //action executed on transition, before state change. int param = transition index in the table
} TBurnTransition;

typedef struct BurnStateConfig {
  TSTATE State;
  char Code;
  void (*fInitialize)(TSTATE s);
  void (*fLoop)();
} TBurnStateConfig;


//initialize the burning automatic algorithm
void initializeBurningLoop();
//periodically run burn control task to handle automatic burning alg.
void burnControlTask();

///functions additional to main boiler control loop
// f.ex. circulation pump
void circulationControlTask();

//wlacz/wylacz tryb automatyczny
void setManualControlMode(bool b);
//wlacz/wylacz tryb reczny z ustawieniem stanu
void setManualControlState(TSTATE t);
//
TSTATE getManualControlState();

//check if heating is needed anywhere (for home or for cwu). 0 - no, 1 - co needed, 2 - cwu needed
HEATNEED needHeatingNow();

///sets alarm state and shows alarm message
void setAlarm(const char* txt);

void forceState(TSTATE st);

void processSensorValues();

int8_t calculateBlowerPowerAdjustment(uint8_t desiredFlow, uint8_t measuredFlow, uint8_t currentBlowerPower);

int firestartIsBurningCheck();
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

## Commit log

2020-02-22 moved burn control out
    [burn_control.cpp, burn_control.h, masterpiec.ino]
2020-02-23 problemy z edycja booli
    [boiler_control.cpp, burn_control.cpp, burn_control.h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]
2022-06-10 problem z ustawieniem recznym stanu
    [ui_screens.cpp]
2022-06-22 attempts at controlling air flow
2022-07-02 pompa bugfix, progmem na struktury statyczne - nie testowany
    [boiler_control.cpp, burn_control.cpp, burn_control.h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]
2022-09-04 hit&miss control of fan/flow
2022-09-21 air flow ctrl
2024-07-25 cwu pompa tryb letni poprawa algorytmu. TODO mozna tez zrobic algo bazujacy na temperaturze powrotu cwu
2025-04-13 external control of furnace and pumps
2025-04-19 external pump control. Warning: works only with setting=2 (low). Want high - need pulldown resistors
2025-06-05 ext control cwu pump delay
2025-09-19 1. tryb letni 2 - nie grzejemy. pin SV2 - sygnalizacja grzania
2025-10-06 dont de-activate on error
    [piec_sensors.cpp]
